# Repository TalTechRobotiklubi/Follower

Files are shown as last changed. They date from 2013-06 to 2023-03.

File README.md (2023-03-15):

Follower
===================
General
-----------
Follower is a robot-platform intended to follow a certain person. The long term goal is to develop a platform, which could act as a personal carrier.
Current repository mainly tracks software, but here are also some documentation.

Concept
-----------
Follower's conceptional drawing is presented below

pilt robotist

The robot has differential drive with two wheels inside the body to avoid collision effect while turning. Sensor boards reads ultrasonic sensors, which should detect any obstacles and inertial measurement unit, which helps to detect robots movements in time (turning, acceleration). Vision board controls servo motors to move camera left/right and up/down.

The robot does not have any basket to carry things. It is a first prototype to 
test following concept.

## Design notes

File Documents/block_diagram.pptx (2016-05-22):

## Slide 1

PC (Zotac)
ensor Board

USB

Kinect ONE

PWM

Servo
ensor Board

2x

USB

VisionBoardr B(STM32F4)

5V

8x

URFs Board

CAN

2 IO

SensorBoard
(STM32F4)
ensor Board

USART

XRF
ensor Board

IMUs Board

USART

5 V

12 V

Motor Controller
ensor Board

Motor Controller
ensor Board

Vbat

Power module
ensor Board

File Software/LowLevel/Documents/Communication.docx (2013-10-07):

TTÜ Robotiklubi MTÜ

12

ITKiller kommunikatsioon

Kommunikatsiooniprotokoll

TTÜ Robotiklubi MTÜ

Sisukord

# Arhitektuur

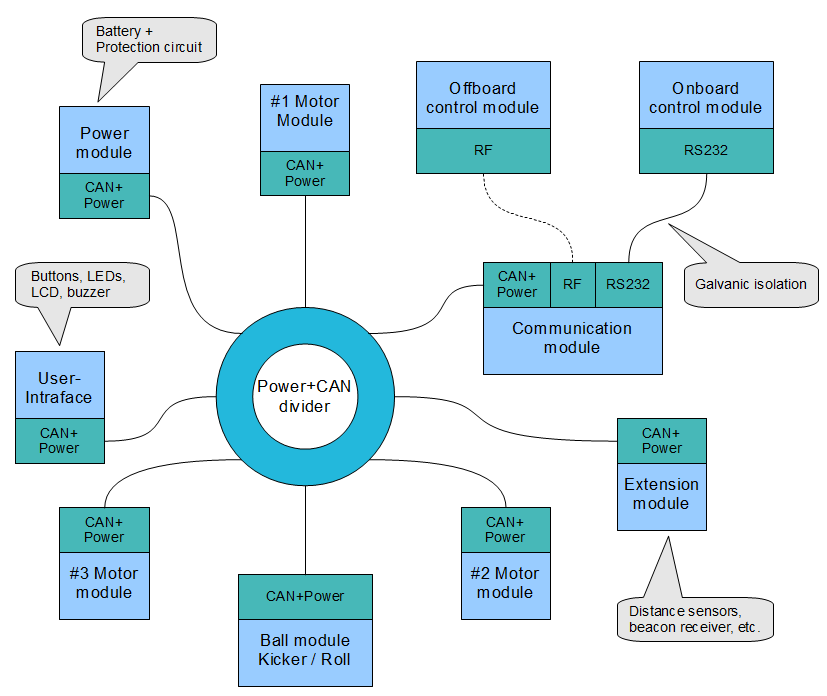
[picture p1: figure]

Roboti “targad” moodulid suhtlevad omavahel CAN siinil. Et PC saaks CAN-iga ühendada, on CAN siinil spetsiaalne kommunikatsioonimoodul mis teisendab CAN sõnumid UART sõnumiteks ja vastupidi:

UART
Kommunikatsiooni-moodul
CAN
PC

UART siinil on kommunikatsiooniprotokolli aluseks võetud CAN. Ehk teisisõnu UART siinil edastatakse peaaegu sama struktuuri ja sisuga sõnumeid nagu CAN siinil. Vahe on ainult sõnumi paketi ülesehituses, mis CAN-i puhul on standardiga ära määratud, UART-i puhul tehtud selles dokumendis.

## CAN liides

Kasutusel on CAN 2.0A standard. Seega ID väli on 11 bitine, kuid kasutatal on sellest ainult 8 madalamat bitti. Kolm kõrgemat bitti on 0. Bitikiirus on 250 kbit/s. Sampling point 75%.

## Jadaliidese

UART/RS232 siinil edastatakse mõlemas suunas samasuguse ehitusega pakette. Pakett mis on saadetud PC-st jadaliidese kaudu CAN siinile, sealt tagasi ei saadeta (ei peegeldu).

Bait | Sisu | Väärtus
0 | Preambula | 0xAA
1 | Sõnumi ID | 0x00 - 0xFF
3 | Sisu pikkus baitides (N) | 1-8
4 | Sisu, ehk signaalid (1..N baiti) | N * 0x00 – 0xFF
5
…
3+N
4+N | Kontrollsumma (16-bit CRC) | 0x00 – 0xFFFF
5+N

Preambula (väärtus 0xAA) on kasutusel sõnumi alguse leidmiseks jadaliidese andmevoost. Preambulale järgneb sõnumi identifikaator (ID) mis on üks-ühele vastavuses CAN sõnumite ID väljaga (8 madalamat bitti sellest). Sõnumi sisu pikkus on 1 bait, millel võib olla väärtuseks 1-8, muul juhul loetakse sõnum vigaseks. Sõnumi sisu on määratud sõnumi ID-ga. Sisus peab olema niipalju baite kui pikkuses kirjas on.

Paketi lõpus on kogu kontrollsumma, millesse arvutatakse sisse sõnumi ID, sisu pikkus ja sisu baidid. CRC algoritm on veel defineerimisel. Arvutatud kontrollsumma ja paketis sisalduvad kontrollsumma mittekattumisel sõnumit ignoreeritakse.

## Sõnumid ja signaalid

Sõnumitel puudub saatja ja addressaat, selle asemel on sõnumil identifikaator (ID) mille alusel sõnumit ja selle sisu tuvastada. CAN ja UART siinil jõuavad kõik sõnumid kõigi mooduliteni. Iga moodul otsustab kas ta on sõnumist huvitatud või mitte. Üldjuhul on siiski määratud mis moodul mis sõnumit saadab.

Sõnumi sisuks on signaalid, ehk ainuühikulised andmed. Signaal võib olla näiteks nupu olek, mootori kiirus või midagi muud mis tähistab ühe kindla funktsiooni reaalset või soovitud olekut. Seega saab sõnumitega edastada olekusignaale ja juhtsignaale.

Signaalide andmehulk on bitipõhine ja nende jaoks on sõnumis reserveeritud täpselt vajalik hulk bitte. Sõnumite kirjelduses on signaalide juures märgitud nende algusbitt ja pikkus. Baidis loendatakse bitte alates vanimast. Ehk näiteks 2-bitine signaal, mille algbiti number on 10 asub teise baidi kolmandas ja neljandas bitis. Sõnumist signaali leidmiseks oleks selle mask 0xC00.

Kokku on ühes sõnumis 1-8 baiti, ehk 8-64 bitti. Bitte loendatakse alates nullist.

# Sõnumid

Järgnevalt on loetletud kõik roboti moodulitevahelised sõnumid

ID | Sõnumi nimi | Selgitus | Saatja | Periood
0xD0 | MotorSpeeds | Kolme mootori sõidukiiruse ühissõnum. | PC | 10 ms
0xD1 | Motor1Status | Esimese mootori hetkekiirus, vool, temperatuur. | Mootor 1 | 100 ms
0xD2 | Motor2Status | Teise mootori hetkekiirus, vool, temperatuur. | Mootor 2 | 100 ms
0xD3 | Motor3Status | Kolmanda mootori hetkekiirus, vool, temperatuur. | Mootor 3 | 100 ms
0xD4 | MotorPID | PID konstantide P, I ja Dmääramine | PC | -
0xB0 | BallControl | Pallimooduli juhtsignaalid. | PC | 20 ms
0xB1 | BallStatus | Pallimooduli olekusignaalid. | Pallimoodul | 20 ms
0xB2 | LineStatus | Eesmiste jooneandurite olek | Pallimoodul | 20 ms
0xC0 | UIControls | Nuppude olekusignaalid. | Komm. moodul | 100 ms
0xC1 | UIFeedback | Indikaator LED-ide ja kõlari juhtsignaal. | PC | -
0xC2 | UIScreenClear | Ekraani kustutamine. | PC | -
0xC3 | UIScreenWrite | Ekraanile kirjutamine. | PC | -
0xA0 | PowerStatus | Aku seisukord. | Komm. moodul | 1000 ms
0xF0 | Sensors | Sensorite tulemused | | 20 ms

Iga sõnum on eraldi lahti seletatud. Sõnumi periood näitab aega, mille tagant sõnumit peab (peaks) kindlaksmääratud saatja seda saatma. Perioodid tuleb ka reaalse sideliidese läbilaskevõimega vastavusse seada. Kui moodulid, mis ootavad kindlat sõnumit, ei saa seda 10 kordse nominaalperioodi jooksul võivad nad ohutuse mõttes välja lülituda, seisma jääda vmt. Sõnumeid, millel pole perioodi määratud, saadetakse vastavalt vajadusele.

## 0xD0 - MotorSpeeds

Mootorite kiiruste seadmise sõnum.

Bitt | Pikkus | Tüüp | Ühik | Signaali nimi | Selgitus
0 | 16 | int16 | rpm | Motor1RequestSpeed | Mootori 1 soovitud pöörlemiskiirus
16 | 16 | int16 | rpm | Motor2RequestSpeed | Mootori 2 soovitud pöörlemiskiirus
32 | 16 | int16 | rpm | Motor3RequestSpeed | Mootori 3 soovitud pöörlemiskiirus

Mootorid on eeldatud asetsema järgneva joonise alusel, kus joon keskel näitab roboti eeldatavat edasiliikumise suunda. Mootorite pöörlemise positiivne suund määratakse parema käe reegliga, kus mootorist ümbert kinni võttes pöial osutab ratta poole ning ülejäänud sõrmed näitavad positiivset pöörlemise suunda. Negatiivne pöörlemise suund on vastupidine positiivsele.

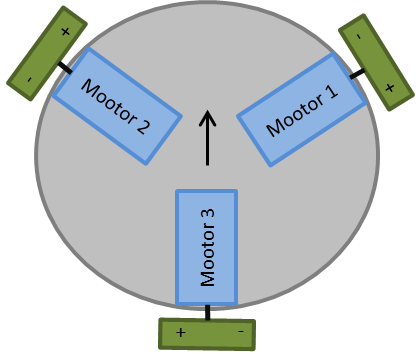
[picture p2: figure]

Mootorite kiiruse sõnumis on kolm 16-bitist signaali, mis tähistavad mootori (mitte ratta) pöörlemiskiirust väärtustes -32768 kuni +32767. Pluss tähistab positiivset pöörlemiskiirust, miinus tähistab negatiivset pöörlemiskiirust. Reaalselt saavutatav kiirus on loomulikult madalam ja see peaks olema tarkvaras konstandina kirjas.

## 0xD1 – Motor1Status, 0xD2 – Motor2Status ja 0xD3 – Motor3Status

Mootori staatuse kirjeldamise sõnum. Kõigis sõnumites on signaalidel samad nimed, aga mootorite indeksid on kas 1, 2 või 3.

Bitt | Pikkus | Tüüp | Ühik | Signaali nimi | Selgitus
0 | 16 | int16 | rpm | Motor1ActualSpeed | Mootori 1 reaalne pöörlemiskiirus
16 | 16 | Int16 | - | Motor1EncoderClicks | Mootori 1 enkoodri muutus viimasest sõnumist.
32 | 8 | uint8 | 100 mA | Motor1CurrentDraw | Mootori 1 voolutarve
40 | 8 | uint8 | °C | Motor1DriverTemp | Mootorikontrolleri 1 temperatuur
48 | 1 | bool | T/F | Motor1BridgeAFault | Mootorikontrolleri 1 poolsilla A viga
49 | 1 | bool | T/F | Motor1BridgeBFault | Mootorikontrolleri 1 poolsilla B viga
50 | 6 | - | - | - | Reserveeritud diagnostikaks

Kolm mootorite olekusõnumit on samasuguse ülesehitusega. Sõnumite signaalid annavad infot mootorite töö kohta. Voolutarve on 100 mA ühikutes, ehk binaarväärtusele 35 vastaks 3,5A.

## 0xD4 - MotorPID

Mootoritele PID konstantide P, I ja D seadmine.

Bitt | Pikkus | Tüüp | Ühik | Signaali nimi | Selgitus
0 | 32 | uint32 | - | ConstantAddress | STM32 kontrolleri mälu aadress
32 | 32 | uint32 | - | ConstantValue | P, I või D väärtus

## 0xB0 – BallControl

Pallimooduli juhtsignaalid.

Bitt | Pikkus | Tüüp | Ühik | Signaali nimi | Selgitus
0 | 1 | bool | T/F | BallCharge | Kondesaatori laadimise lubamine.
1 | 7 | uint8 | % | BallDribblerPower | Rullimootori PWM tööaeg.
8 | 10 | uint16 | ms | BallKickTime | Solenoidi löögiaeg.
18 | 1 | bool | T/F | BallKick | Solenoid löömine.

BallCharge kaudu juhitakse kondensaatori laadimisskeemi tööd. Tõese väärtus (1) puhul on automaatne laadimine lubatud, väära (0) puhul mitte. Kui laadimine keelatakse, siis kondensaatori laadimine peatatakse, kuid seda ei tühjendata.

BallKick kaudu antakse käsk palli löömiseks solenoidiga. Tõese väärtus (1) puhul on palli löömiskäsk antud, väära (0) puhul mitte. Kui väärtus jätta tõeseks, siis tehakse löök automaatselt kondensaatori laadimise lõppedes. Seega ühekordseks löögiks peab väärtuse enne laadimise lõppemist ära nullima.

BallKickTime kaudu määratakse solenoidi transistori lahtioleku aeg. See mõjutab löögi aega ja tugevust. Väärtus on 0-1023 millisekundit.

BallDribblerPower määrab rulli mootori töötsükli aja protsentides. Väärtuse 0 puhul mootor seisab, väärtuse 100 (või suurema) puhul töötab maksimaalse võimsusega.

## 0xB1 – BallStatus

Pallimooduli olekusignaalid.

Bitt | Pikkus | Tüüp | Ühik | Signaali nimi | Selgitus
0 | 1 | bool | T/F | BallContact | Rullianduri olek (kontakt palliga).
1 | 1 | bool | T/F | BallInSight | Optilise palli anduri olek.
2 | 1 | bool | T/F | BallCapacitorCharged | Kondensaatori laetuse olek.

BallContact näitab kas pall (või muu objekt) on rulli all. Tõene väärtus (1) puhul on rull tõusnud, 0 (False) puhul mitte.

BallInSight on optilise pallianduri olek. Optiline andur peaks nägema palli mõned sentimeetrid enne rulli. Tõene väärtus (1) näitab, et palliandur näeb palli või muud objekti, väär (0) vastupidist.

BallCapacitorCharged on löögielektroonika kondensaatori laetuse olek. Tõese väärtuse (1) puhul on kondensaator täielikult laetud, väära (0) puhul (veel) mitte.

## 0xB2 – LineStatus

Jooneandurite olekusignaalid.

Bitt | Pikkus | Tüüp | Ühik | Signaali nimi | Selgitus
0 | 8 | uint8 | % | LineLeftIntensity | Vasaku jooneanduri intensiivsus.
8 | 8 | uint8 | % | LineRightIntensity | Parema jooneanduri intensiivsus.

LineLeftIntensity ja LineRightIntensity näitavad optilistesse peegeldusanduritesse tagasipeegeldunud valguse intensiivust. Väärtuse 0% puhul on valguse intensiivsus minimaalne (optotransistor on suletud), väärtuse 100% puhul on valguse intensiivsus maksimaalne (optotransistor on täielikult avatud).

## 0xC0 – UIControls

Juhtpaneeli juhtliideste olekud.

Bitt | Pikkus | Tüüp | Ühik | Signaali nimi | Selgitus
0 | 1 | bool | T/F | ButtonTopLeft | Ülemise vasaku nupu olek.
1 | 1 | bool | T/F | ButtonTopRight | Ülemise parema nupu olek.
2 | 1 | bool | T/F | ButtonBottomLeft | Alumise vasaku nupu olek.
3 | 1 | bool | T/F | ButtonBottomRight | Alumise parema nupu olek.

ButtonTopLeft, ButtonTopRight, ButtonBottomLeft ja ButtonBottomRight on kommunikatsioonimooduli paneelil olevate nuppude olekud. Tõese väärtuse (1) puhul on nupp alla vajutatud, väära (0) puhul mitte.

## 0xC1 – UIFeedback

Juhtpaneeli tagasisidefunktsioonide käsud.

Bitt | Pikkus | Tüüp | Ühik | Signaali nimi | Selgitus
0 | 8 | uint8 | ms | LEDRed | Punase valgusdioodi põlemise aeg.
8 | 8 | uint8 | ms | LEDGreen | Rohelise valgusdioodi põlemise aeg.
16 | 16 | uint16 | Hz | BeepFrequency | Piiksu sagedus.
32 | 8 | uint8 | ms | BeepDuration | Piiksu pikkus.

LEDRed ja LEDGreen signaalid juhivad vastavalt punase ja rohelise valgusdioodi põlemise aega. Väärtuste 1 ms ja suuremate puhul põleb valgusdiood vastava aja alates sõnumi kättesaamisest. Väärtuse 0 puhul valgusdioodi ei juhita, ehk sellega saab lasta eelmisel valgusdioodi käsul edasi toimida.

BeepFrequency määrab ära soovitud helisignaali sageduse. Väärtus on 0 kuni 65535 hz, kuid loomulikult sõltub saavutatav helikõrgus kõlarist. Reaalne väärtus on 500 hz kuni 5000 hz.

BeepDuration määrab kas teha helisignaal (piiks) ja kui pikk. Väärtuse 1 ms ja suuremate väärtuste puhul kostab signaal vastava aja alates sõnumi saabumisest. Väärtuse 0 puhul heli ei tehta ja kui sõnumi saabumisel pole eelmine helisignaal lõppenud, siis seda ei peatata kah. Kui eelmine helisignaal pole lõppenud ja tuleb käsk uue jaoks, siis alustatakse koheselt uue signaaliga.

NB. Aku tühjenemise korral võib juhtmoodul helisignaali käskusid ignoreerida ja kasutada automaatset hoiatussignaali.

## 0xC2 – UIScreenClear

Juhtpaneeli ekraanil rea kustutamise sõnum. Kokku on ekraanil 4 rida.

Bitt | Pikkus | Tüüp | Ühik | Signaali nimi | Selgitus
0 | 3 | uint8 | - | ScreenRow | Ekraani rea number.

ScreenRow näitab rida, mis tekstist kustutada. Väärtuste 0 kuni 3 puhul kustutatakse rida 1 kuni 4. Ridasid loetakse ülevalt alla. Väärtuse 4 kuni 7 korral kustutatakse kogu ekraan.

## 0xC3 – UIScreenWrite

Juhtpaneeli ekraanile teksti kirjutamise sõnum. Ekraanile mahub 4 rida 16-märgist ASCII kodeeringus teksti. Teksti saab vanast tekstist üle kirjutada.

Bitt | Pikkus | Tüüp | Ühik | Signaali nimi | Selgitus
0 | 4 | uint8 | - | ScreenRow | Ekraani rea number.
4 | 4 | uint8 | - | ScreenColumn | Ekraani tulba number.
8 | 4 | uint8 | - | ScreenTextLen | Teksti pikkus mida kirjutada (1-6)
16 | 48 | char | | ScreenText | Tekst (6 märki)

ScreenRow näitab rida millele tekst kirjutada. Väärtused 0 kuni 3 tähistavad ridu 1 kuni 4. Ridasid loetakse ülevalt alla.

ScreenColumn näitab tulpa millest alates teksti kirjutada. Tulpasid loetakse vasakult.

ScreenTextLen näitab mitu märki sõnumis olevast tekstist ekraanile kirjutada. Kuna sõnumi pikkus on deterministlikusse säilitamiseks fikseeritud, siis pikkust määrab see signaal. Väärtuse 0 puhul kirjutatakse ekraanile üks (esimene) märk, väärtuse 5 (või suurem) puhul kõik 6 märki.

ScreenText sisaldab ASCII kodeeringus 6-märgilist teksti. Kui kirjutatada soovitakse vähem kui 6 märki, siis ülejäänud märgid võivad olla 0xFF. Seda kas kasutada saab kogu ASCII tabelit, sõltub kommunikatsioonimoodulist. Suur ja väike ladina tähestik, numbrid ja kirjavahemärgid peaksid kindlasti toetatud olema.

## 0xA0 - PowerStatus

Aku seisundi olekusõnum.

Bitt | Pikkus | Tüüp | Ühik | Signaali nimi | Selgitus
0 | 16 | uint16 | mV | Battery1Voltage | Aku 1 (mootorite aku) pinge.

Battery1Voltage näitab aku 100 ms jooksul keskmistatud pinget. Väärtused on 0 kuni 65535 mV.

## 0xF0 – Sensors

Sensorite näitude sõnum.

Bitt | Pikkus | Tüüp | Ühik | Signaali nimi | Selgitus
0 | 8 | uint8 | cm | DistanceSensor1 | Distantsisensori 1 kaugusnäit.
8 | 8 | uint8 | cm | DistanceSensor2 | Distantsisensori 2 kaugusnäit.
16 | 8 | uint8 | cm | DistanceSensor3 | Distantsisensori 3 kaugusnäit.
24 | 8 | uint8 | cm | DistanceSensor4 | Distantsisensori 4 kaugusnäit.
32 | 8 | uint8 | cm | DistanceSensor5 | Distantsisensori 5 kaugusnäit.
40 | 8 | uint8 | cm | DistanceSensor6 | Distantsisensori 6 kaugusnäit.
48 | 8 | uint8 | cm | DistanceSensor7 | Distantsisensori 7 kaugusnäit.
56 | 8 | uint8 | cm | DistanceSensor8 | Distantsisensori 8 kaugusnäit.

Distancesensor signaal näitab kaugust sentimeetrites.

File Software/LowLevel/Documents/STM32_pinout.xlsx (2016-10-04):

 |  |  |  |  |  |  |  |  |  | free
 |  |  |  |  |  |  |  |  |  | occupied by kit
 |  |  |  |  |  |  |  |  |  | used by follower
 |  |  |  |  |  |  |  |  |  | occupied by kit / used by follower
 |  |  | STM32 pinout
follower | kit function |  |  |  | follower | follower | kit function |  |  | kit function | follower
 |  | GND | GND |  |  |  |  | GND | GND
 |  | VDD | VDD |  |  |  |  | 5V | 5V
 |  | GND | NRST |  |  |  |  | 3V | 3V
 |  | PC1 | PC0 |  |  |  | OSC_IN | PH0 | PH1 | OSC_OUT
 |  | PC3 | PC2 |  |  | URF1 echo |  | PC14 | PC15 |  | URF1 trig
 |  | PA1 | PA0 | user button |  | URF2 echo |  | PE6 | PC13 |  | URF2 trig |  |  | xRF
USART2_RX / XRF_Rx |  | PA3 | PA2 |  | USART2_TX / XRF_Tx | URF3 echo |  | PE4 | PE5 |  | URF3 trig |  |  | pin 2 | receive
 | acceler SPI | PA5 | PA4 |  |  | URF4 echo |  | PE2 | PE3 | CS_I2C/SPI |  |  |  | pin 3 | transmit
 | acceler SPI | PA7 | PA6 | acceler SPI |  |  | acceler INT1 | PE0 | PE1 | acceler INT2
URF5 echo |  | PC5 | PC4 |  | URF5 trig | URF4 trig |  | PB8 | PB9 | I2C1_SDA
URF6 echo |  | PB1 | PB0 |  | URF6 trig |  |  | BOOT0 | VDD
 |  | GND | PB2 |  |  |  | I2C1_SCL | PB6 | PB7 |  |  |  |  | XRF plaat top view
URF7 echo |  | PE7 | PE8 |  | URF7 trig |  |  | PB4 | PB5 |  |  | 1 | 2 | 3 | 4 | 5 | 6 | 7 | 8
URF8 echo |  | PE9 | PE10 |  | URF8 trig |  |  | PD7 | PB3 |  |  | gnd |  | Rx | Tx | gnd | 3,3V
 |  | PE11 | PE12 |  |  |  |  | PD5 | PD6
 |  | PE13 | PE14 |  |  |  |  | PD3 | PD4 | reset
 |  | PE15 | PB10 |  |  | CAN1_Tx |  | PD1 | PD2
 |  | PB11 | PB12 |  |  |  |  | PC12 | PD0 |  | CAN1_Rx
 |  | PB13 | PB14 |  |  | UART4_Tx | SCLK | PC10 | PC11 |  | UART4_Rx |  |  |  | XRF
 |  | PB15 | PD8 |  |  |  |  | PA14 | PA15
 |  | PD9 | PD10 |  |  |  |  | PA10 | PA13
 |  | PD11 | PD12 | green LED |  |  | I2C3_SCL | PA8 | PA9 | Vbus green LED
 | orange LED | PD13 | PD14 | red LED |  | stop switch |  | PC8 | PC9 | I2C3_SDA
 | blue LED | PD15 | NC |  |  |  |  | PC6 | PC7 | CS43L22 MCLK
 |  | GND | GND |  |  |  |  | GND | GND

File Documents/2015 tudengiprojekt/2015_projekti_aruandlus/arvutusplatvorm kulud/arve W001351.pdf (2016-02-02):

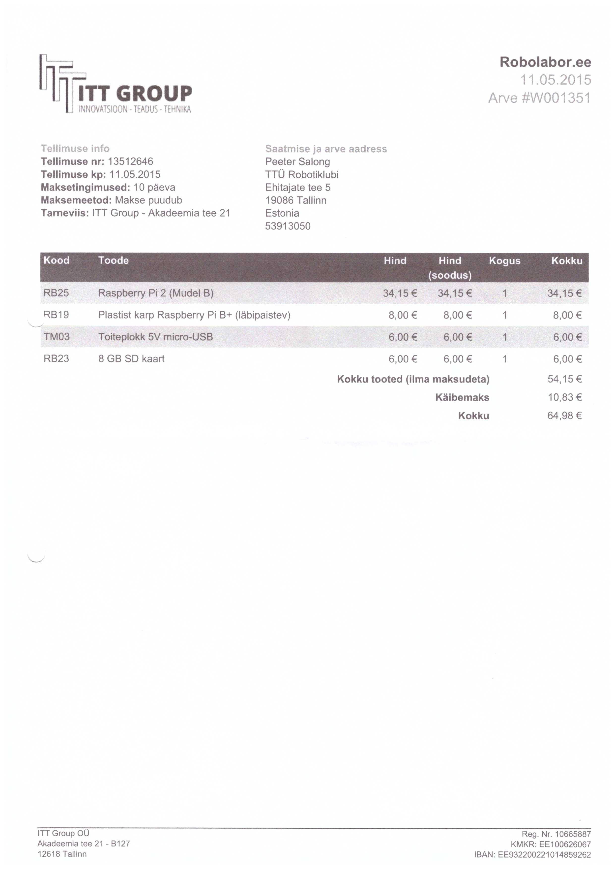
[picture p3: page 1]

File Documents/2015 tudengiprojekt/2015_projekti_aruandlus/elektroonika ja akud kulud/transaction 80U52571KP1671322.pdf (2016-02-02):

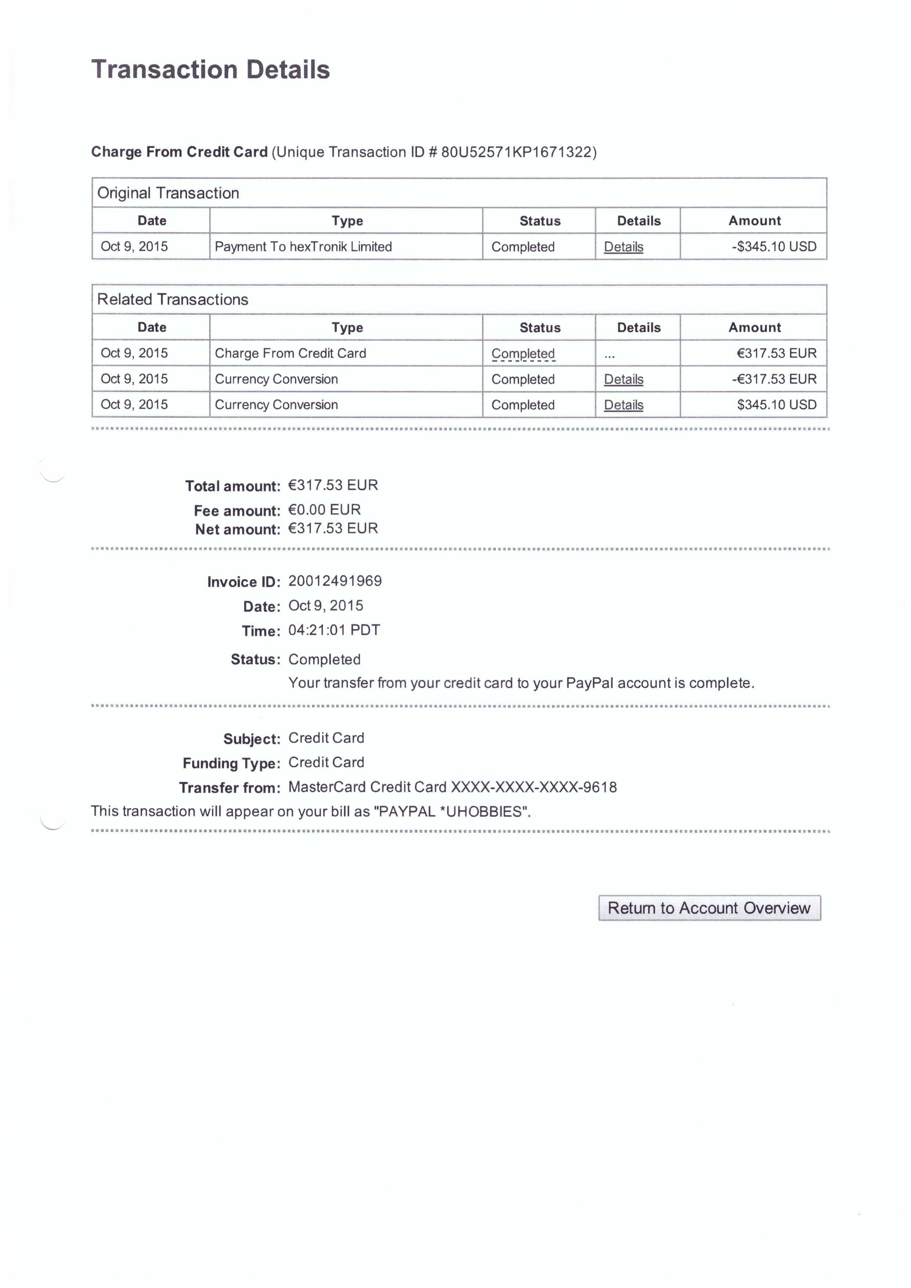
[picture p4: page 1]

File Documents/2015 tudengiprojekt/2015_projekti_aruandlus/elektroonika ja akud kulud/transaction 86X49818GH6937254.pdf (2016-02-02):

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

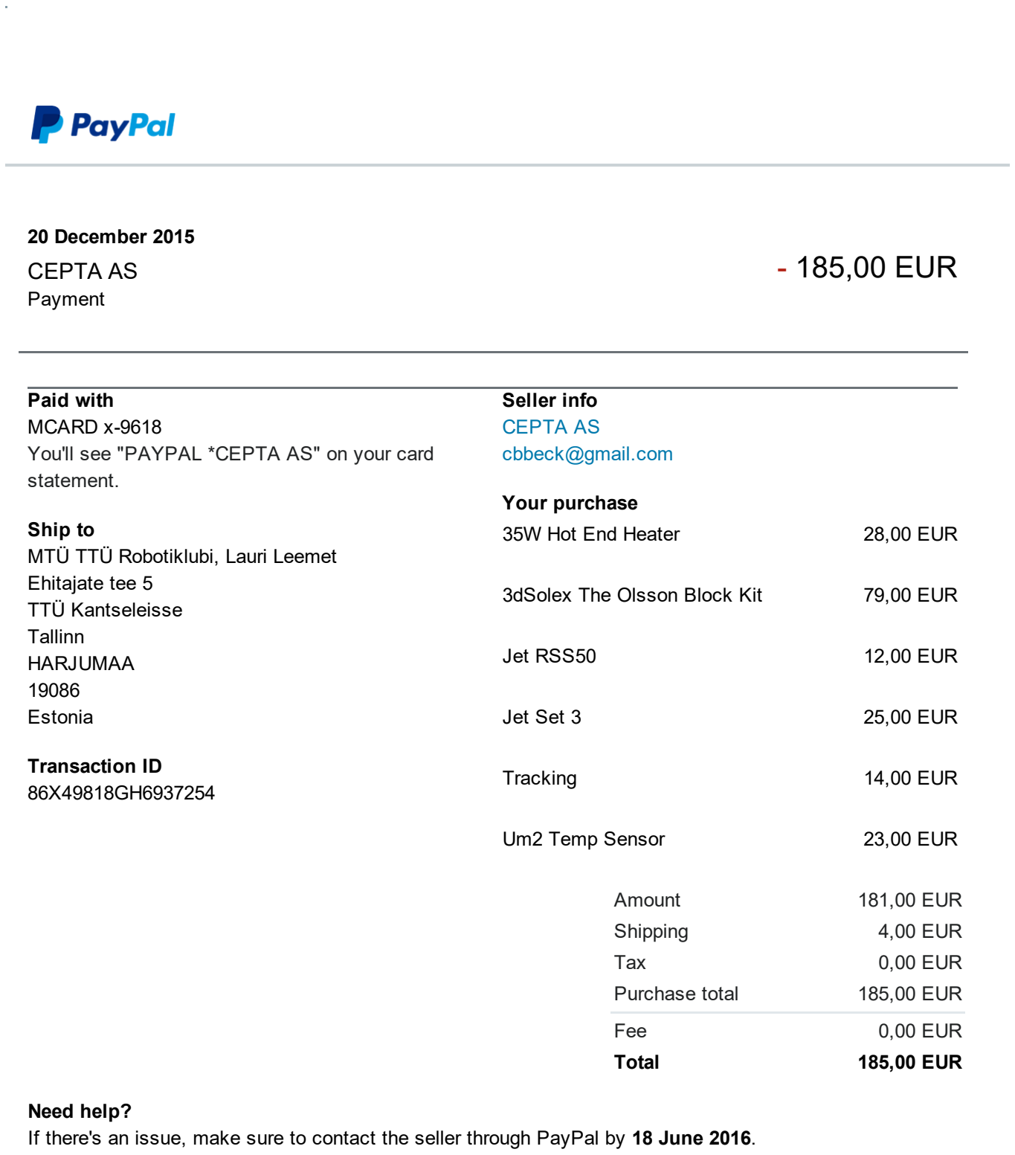
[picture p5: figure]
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

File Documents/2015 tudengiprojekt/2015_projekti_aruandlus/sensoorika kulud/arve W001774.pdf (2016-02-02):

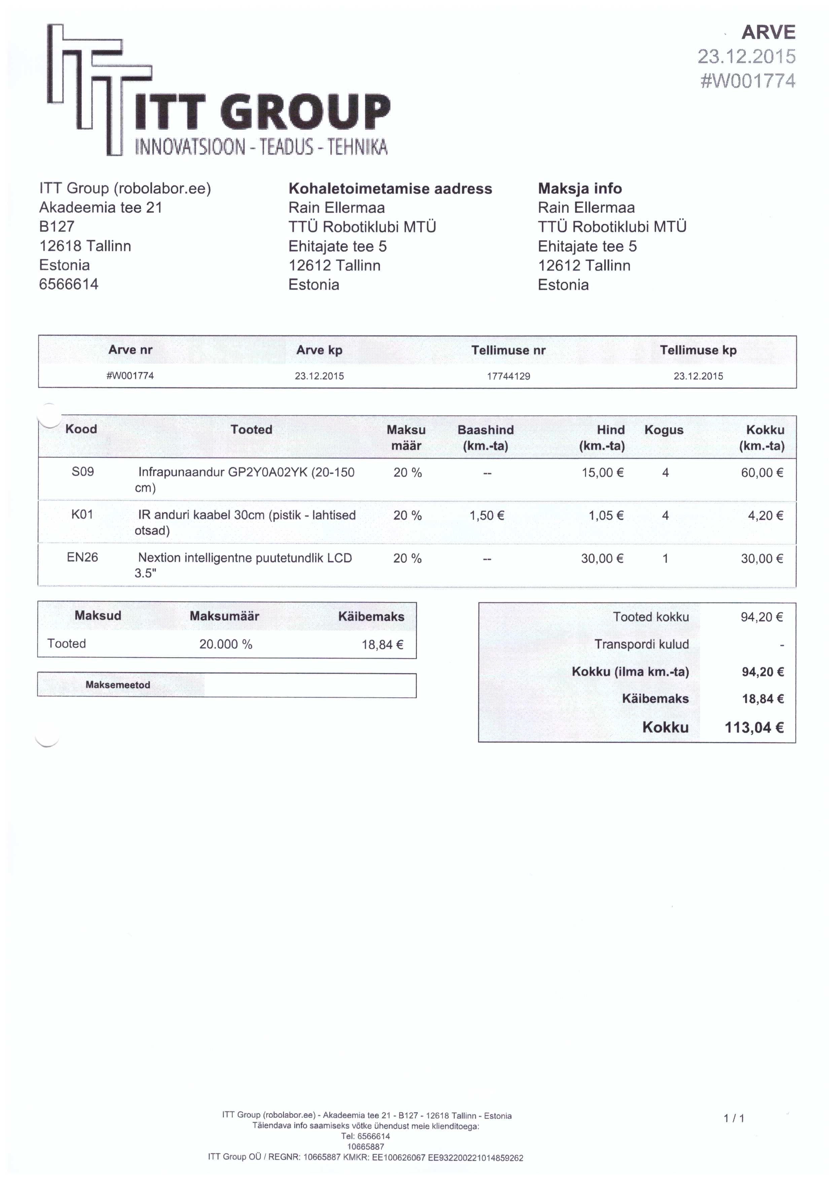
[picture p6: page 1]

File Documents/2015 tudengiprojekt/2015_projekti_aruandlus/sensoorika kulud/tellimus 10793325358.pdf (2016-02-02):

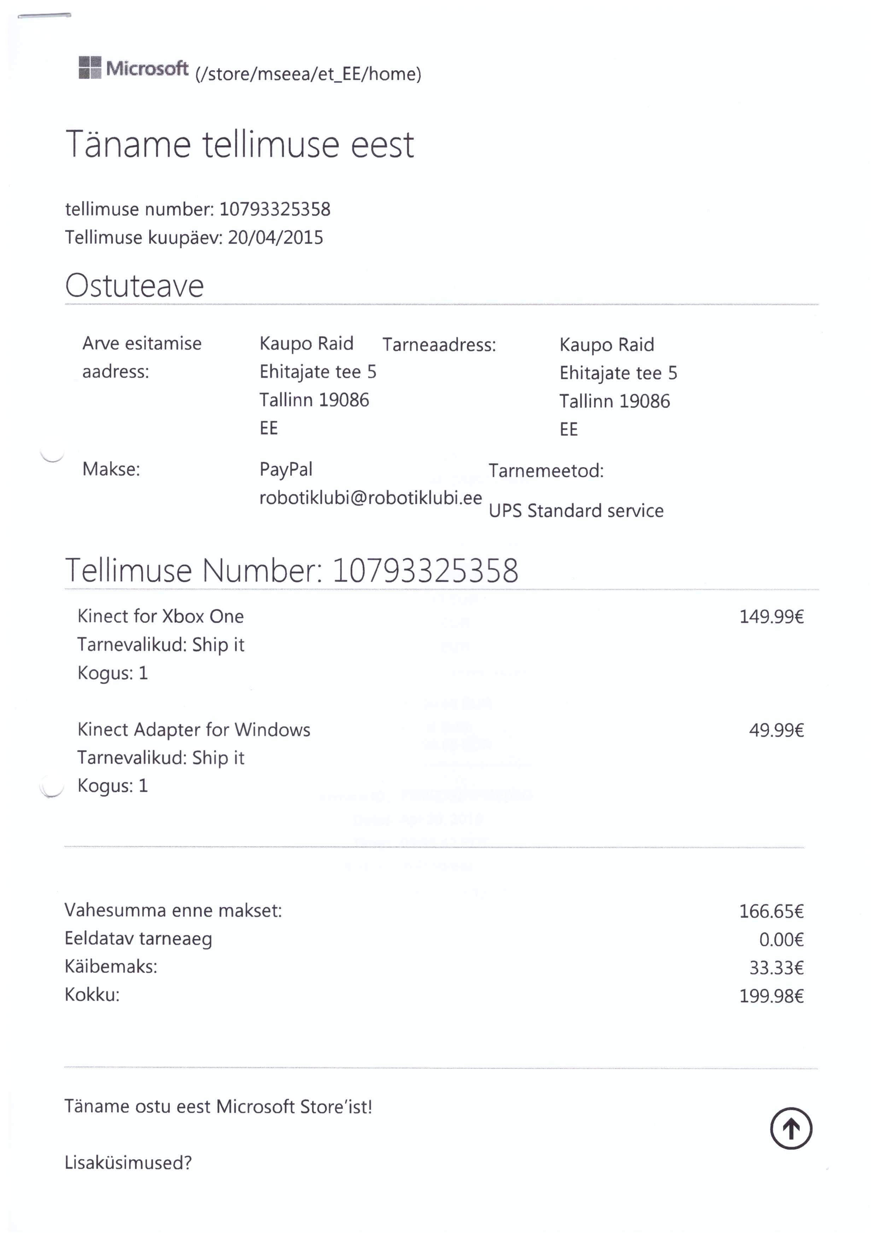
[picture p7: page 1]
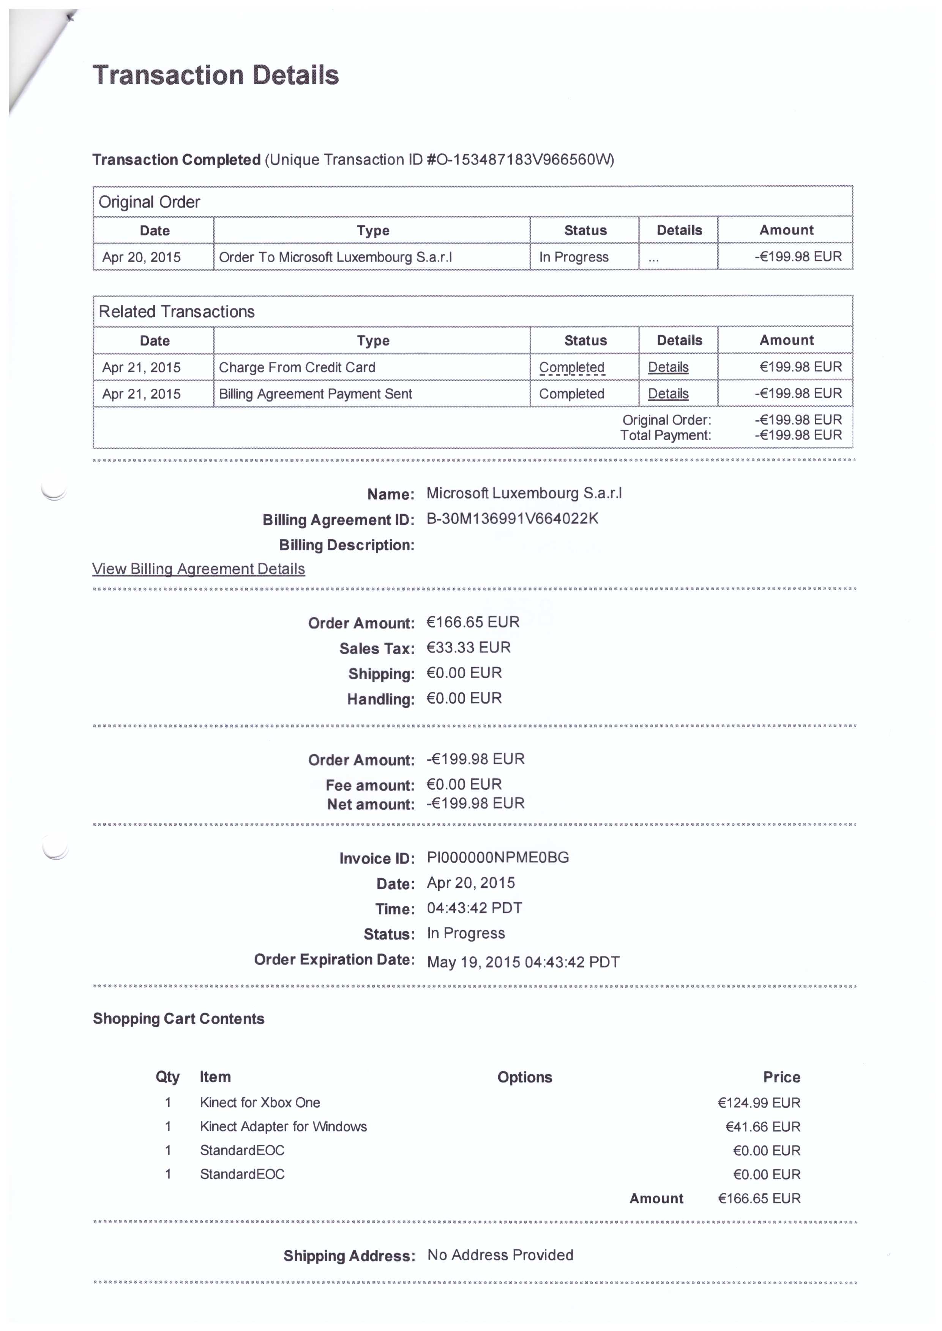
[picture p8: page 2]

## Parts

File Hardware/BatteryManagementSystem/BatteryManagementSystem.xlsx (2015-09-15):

 | LiPo Battery management system
 | Rain Ellermaa
 | BatteryManagementSystem.PrjPCB
 | None
 | 4.05.2014 | 22:23:08
 | 2014-05-04 | 23:50:14
Nr | Description | Comment | Designator | Footprint | Manufacturer | ManufacturerPN | FarnellPN | Quantity | Unit Price | Part Price
1 | Capacitor Ceramic | 1uF | C1B, C2B, C13C, C14C, C15C | C 0603 |  | MC0603X105K250CT | 1759409 | 5 | 0.026 € | 0.130 €
2 | Capacitor Ceramic | 10uF | C1C, C2C, C5C, C8C, C9C, C20C | C 1206 |  | MC1206X106K250CT | 2320887 | 6 | 0.121 € | 0.726 €
3 | Capacitor Ceramic | 100pF | C3B, C4B | C 0603 |  | MC0603N101J500CT | 1759066 | 2 | 0.010 € | 0.020 €
4 | Capacitor Ceramic | 100nF | C3C, C4C, C5B, C6B, C6C, C7B, C7C, C8B, C9B, C10B, C10C, C11B, C12B, C12C, C13B, C17C, C18C, C19C | C 0402 |  |  |  | 18 |  | 0.000 €
5 | Capacitor Ceramic | 56nF | C11C, C16C | C 0603 |  | C0603C563K5RACTU | 1865538 | 2 | 0.014 € | 0.028 €
6 | Capacitor Ceramic | 2.2uF | C21C | C 0805 |  | GRM21BF51E225ZA01L | 9527702 | 1 | 0.105 € | 0.105 €
7 | Diode | BAT54HT1G | D1B, D1C, D2B | SOD323 |  | 1PS76SB10 | 1081179 | 3 | 0.390 € | 1.170 €
8 | LED | Charge in progress | D2C | LED 3.2x1.6 |  | KPT-2012SURCK | 2099241 | 1 | 0.085 € | 0.085 €
9 | Diode Zener | 5.6V | D3B | SOD323 |  | BZT52C5V6S-7-F | 2077936 | 1 | 0.035 € | 0.035 €
10 | LED | Charge complete | D3C | LED 3.2x1.6 |  | KPT-2012SGC | 2099239 | 1 | 0.069 € | 0.069 €
11 | LED | Power good | D4C | LED 3.2x1.6 |  | KP-2012QBC-D | 2217974 | 1 | 0.169 € | 0.169 €
12 | Inductor | 6.8uH | L1C | COIL5 |  | SRP1235-6R8M | 1828109 | 1 | 1.590 € | 1.590 €
13 | Header, 4-Pin | NTC Thermistors | P1B | MHDR1X4 |  | NTCLE203E3103GB0 | 1187036 | 3 | 1.180 € | 3.540 €
14 | Header, 2-Pin | NTC thermistor | P1C | MHDR1X2 |  | NTCLE203E3103GB0 | 1187036 | 1 |  | 0.000 €
15 | Header, 4-Pin | SMBus | P2BMS | MHDR1X4 |  |  |  | 1 |  | 0.000 €
16 | Header, 4-Pin, Right Angle | Balancer | P2L | HDR1X4H |  |  |  | 1 |  | 0.000 €
17 | Resistor | 10k | R1B, R20B, R20C, R21C, R22C, R24C | R 0603 |  |  |  | 6 |  | 0.000 €
18 | Resistor | 0,01R | R1C, R8C | R 1206 |  | LRMAM1206-R01FT5 | 2079442 | 2 | 0.210 € | 0.420 €
19 | Resistor | 100R | R2B, R5B, R6B, R8B, R9B, R10B, R12B, R13B, R13C | R 0603 |  | CRGH0603F100R | 2331989 | 9 | 0.010 € | 0.090 €
20 | Resistor | 2R | R2C | R 1206 |  | MC0125W120612R0 | 2142034 | 1 | 0.061 € | 0.061 €
21 | Resistor | 1k | R3B, R5C, R6C, R7C, R9C | R 0603 |  |  |  | 5 |  | 0.000 €
22 | Resistor | 100k | R3C, R17C, R18C, R19C, R22B | R 0603 |  |  |  | 5 |  | 0.000 €
23 | Resistor | 200R | R4B, R7B | R 0603 |  | CR0603-JW-201GLF | 2333571 | 2 | 0.014 € | 0.028 €
24 | Resistor | 2k | R11B | R 0603 |  | CPF0603F2K0C1 | 1527506 | 1 | 0.049 € | 0.049 €
25 | Resistor | 9,31k | R11C | R 0603 |  | CPF0603F9K31C1 | 1527578 | 1 | 0.049 € | 0.049 €
26 | Resistor | 1M | R12C | R 0603 |  | CRGH0603F1M0 | 2332042 | 1 | 0.010 € | 0.010 €
27 | Resistor | 0,02R | R14B, R15B, R16B, R17B | R 2512 |  | LVK24R020DER | 1462319 | 4 | 1.650 € | 6.600 €
28 | Resistor | 430k | R14C | R 0603 |  | CRCW0603430KFKEA | 2138561 | 1 | 0.007 € | 0.007 €
29 | Resistor | 200k | R15C | R 0603 |  | CR0603-FX-2003ELF | 2333532 | 1 | 0.023 € | 0.023 €
30 | Resistor | 10R | R16C | R 0603 |  | CRGH0603J10R | 2331699 | 1 | 0.008 € | 0.008 €
31 | Resistor | 3M | R18B, R21B | R 0603 |  | MC0063W060313M00 | 2141599 | 2 | 0.029 € | 0.058 €
32 | Resistor | 5.1k | R19B, R23B | R 0603 |  | CR0603-FX-5101ELF | 2333596 | 2 | 0.023 € | 0.046 €
33 | Resistor | 22.1k | R23C | R 0603 |  | CPF0603F22K1C1 | 1527620 | 1 | 0.049 € | 0.049 €
34 | Resistor | 32.4k | R25C | R 0603 |  | ERJ3EKF3242V | 2059455 | 1 | 0.012 € | 0.012 €
35 | Mosfet N-Ch | NTMFS4926NT1G | T1B, T2B, T4C, T5B, T5C, T6B, T7B, T8B | DFN5 |  | NTMFS4926NT1G | 2317608 | 8 | 0.260 € | 2.080 €
36 | Mosfet P-Ch | SI7101DN-T1-GE3 | T1C, T2C | DFN5 |  | SI7101DN-T1-GE3 | 2364059 | 2 | 0.600 € | 1.200 €
37 | Mosfet N-Ch | 2N7002 | T3B | SOT-23 |  | 2N7002 | 1510761 | 1 | 0.039 € | 0.039 €
38 | Mosfet P-Ch | BSS84AK | T4B | SOT-23 |  | BSS84AK | 1972673 | 1 | 0.098 € | 0.098 €
39 | Li-Ion Battery Pack Manager | BQ3055DBTR | U1B | DBT30_N | Texas Instruments |  |  | 1 |  | 0.000 €
40 | Li-Polymer Battery Charger | BQ24610RGER | U1C | RGE24-2450X2450TP | Texas Instruments |  |  | 1 |  | 0.000 €
Total |  |  |  |  |  |  |  |  |  | 18.59 €
 |  |  |  |  |  |  |  |  | Total+KM | 22.31 €

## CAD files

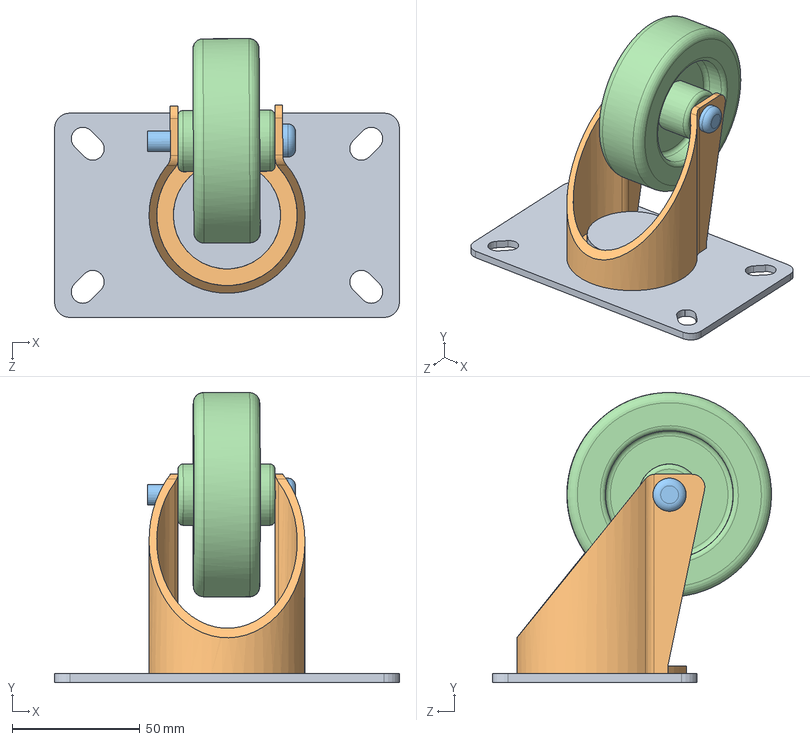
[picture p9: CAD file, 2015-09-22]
Hardware/Body/Esiratas.SLDASM
135.0 x 113.5 x 109.2 mm
Eesratta plaat
Eesratta raam
Eesratta polt
Esiratas

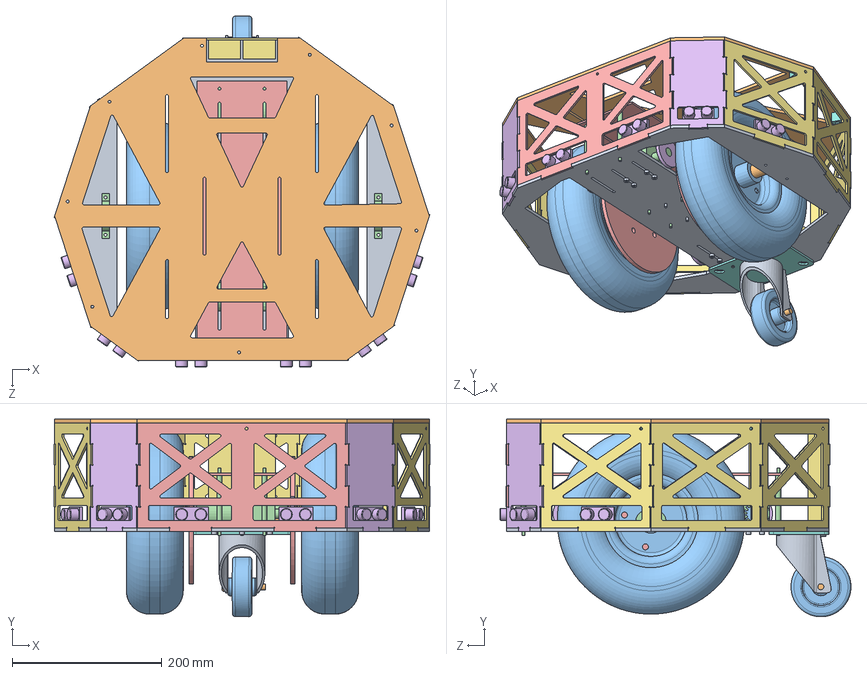
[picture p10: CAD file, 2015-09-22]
Hardware/Body/Koos.SLDASM
501.4 x 263.5 x 468.3 mm
Alus
Telg
Ratas x 2
Mootor x 2
Suur hammasratas x 2
Väike hammasratas x 2
Aku x 2
Eesratta plaat
Eesratta raam
Eesratta polt
Esiratas
Teljekinnitus x 3
Suur külg
Väike külg x 2
Küljeplaat x 7
Kinnitusblokk x 8
4x15 polt x 11
Katus
Enkoodriratas x 2
Sisemine puks x 8
Siseplaat
Ultraheli andur x 6

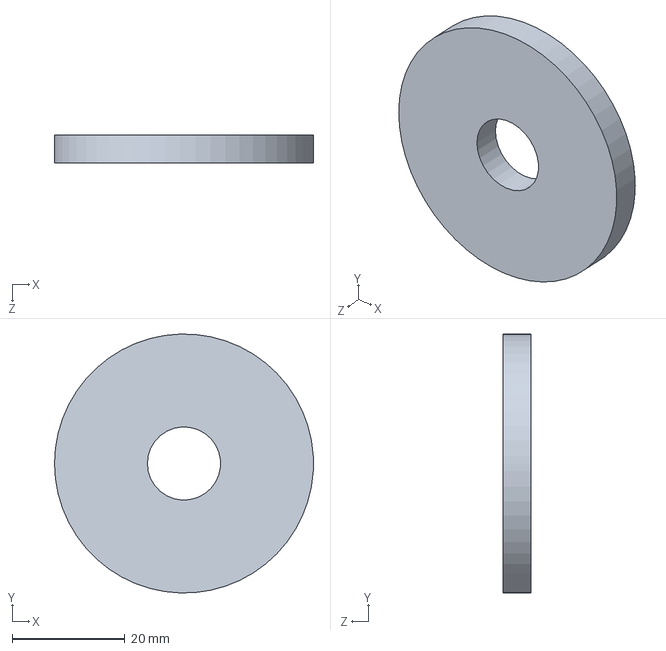
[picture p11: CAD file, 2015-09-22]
Hardware/Body/V�ike hammasratas.SLDPRT
46.0 x 46.0 x 5.00 mm

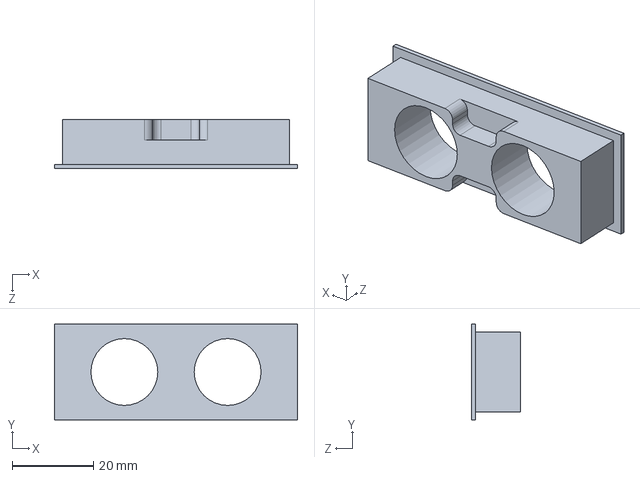
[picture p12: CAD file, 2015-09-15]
Hardware/URF Box/URFBox.SLDPRT
60.0 x 23.7 x 12.0 mm

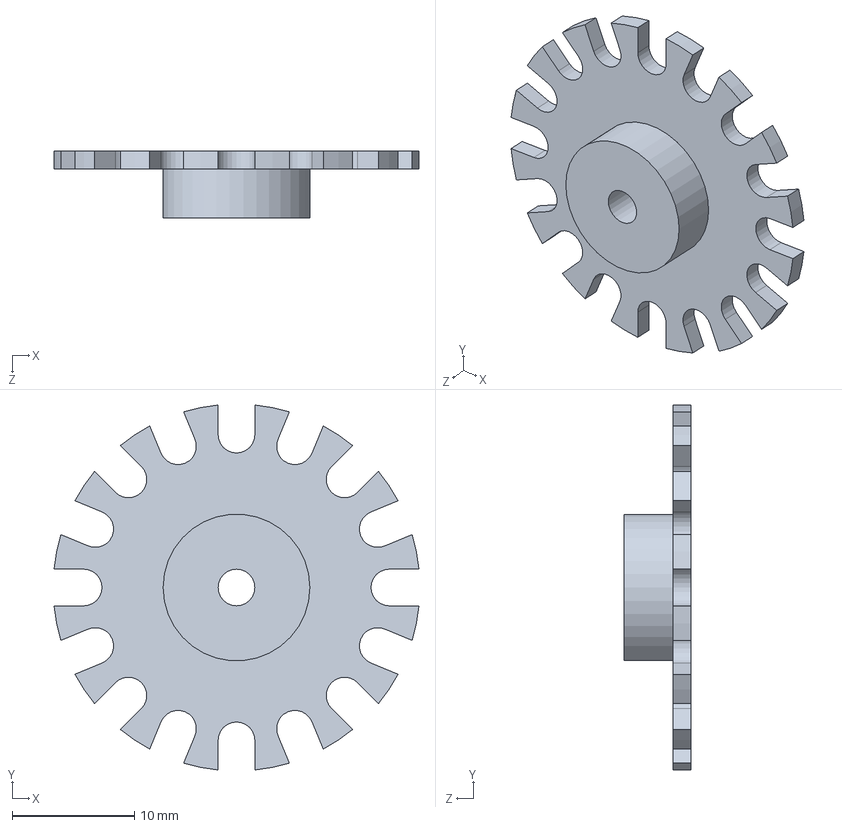
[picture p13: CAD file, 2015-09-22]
Hardware/Body/Enkoodriratas.SLDPRT
29.8 x 29.8 x 5.50 mm

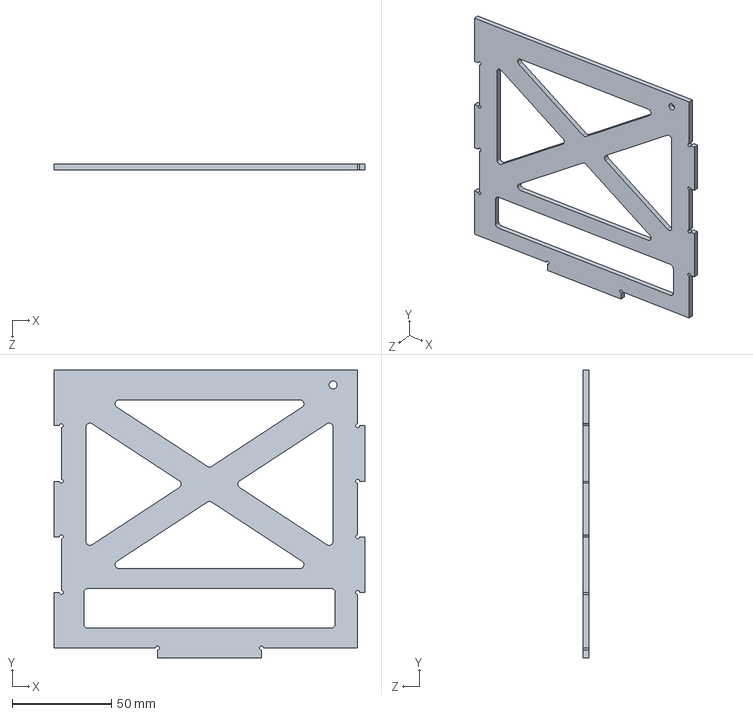
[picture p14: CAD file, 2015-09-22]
Hardware/Body/K�ljeplaat.SLDPRT
156.7 x 145.0 x 3.00 mm

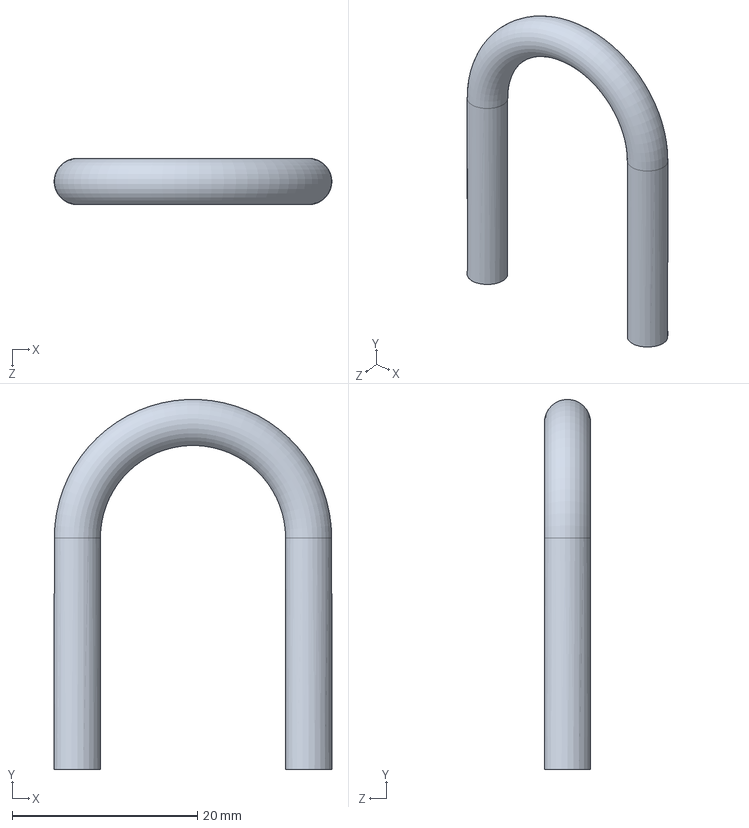
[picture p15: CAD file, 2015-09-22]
Hardware/Body/Teljeklamber.SLDPRT
30.0 x 40.0 x 5.00 mm

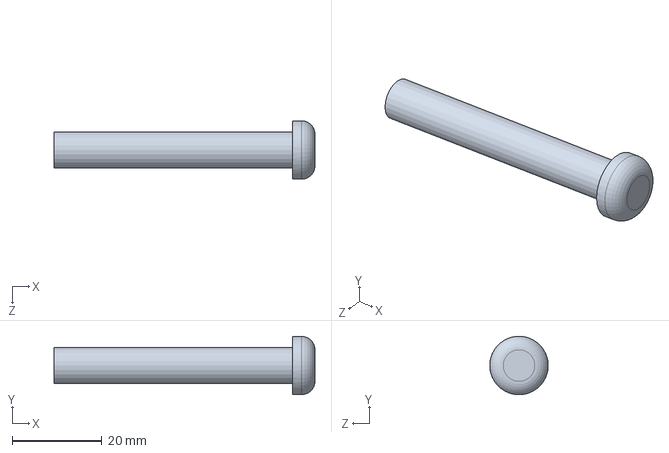
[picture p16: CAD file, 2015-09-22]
Hardware/Body/Eesratta polt.SLDPRT
58.0 x 13.0 x 13.0 mm

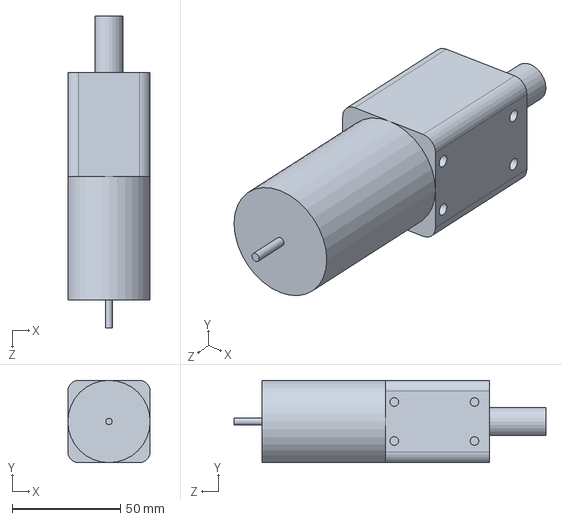
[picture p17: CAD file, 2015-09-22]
Hardware/Body/Mootor.SLDPRT
38.0 x 38.0 x 144.0 mm

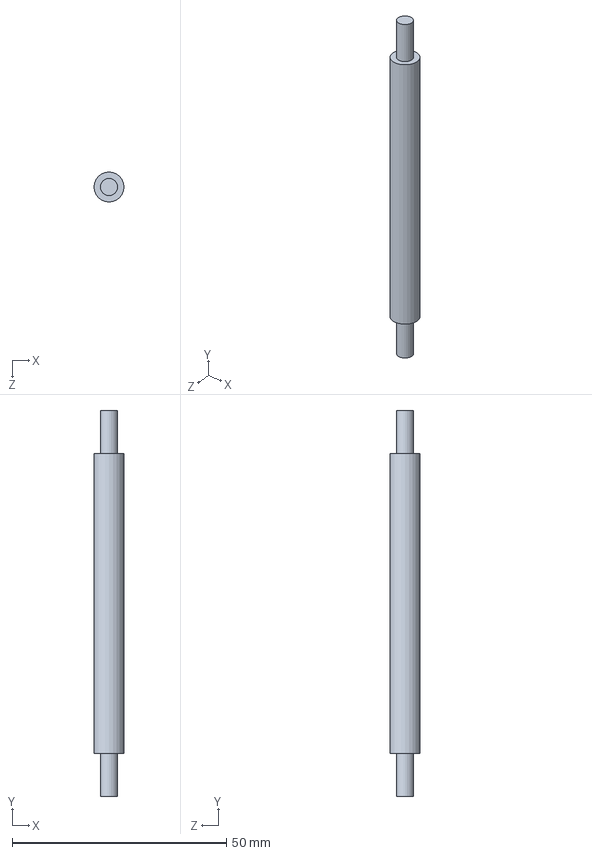
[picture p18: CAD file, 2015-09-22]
Hardware/Body/Sisemine puks.SLDPRT
7.00 x 90.0 x 7.00 mm

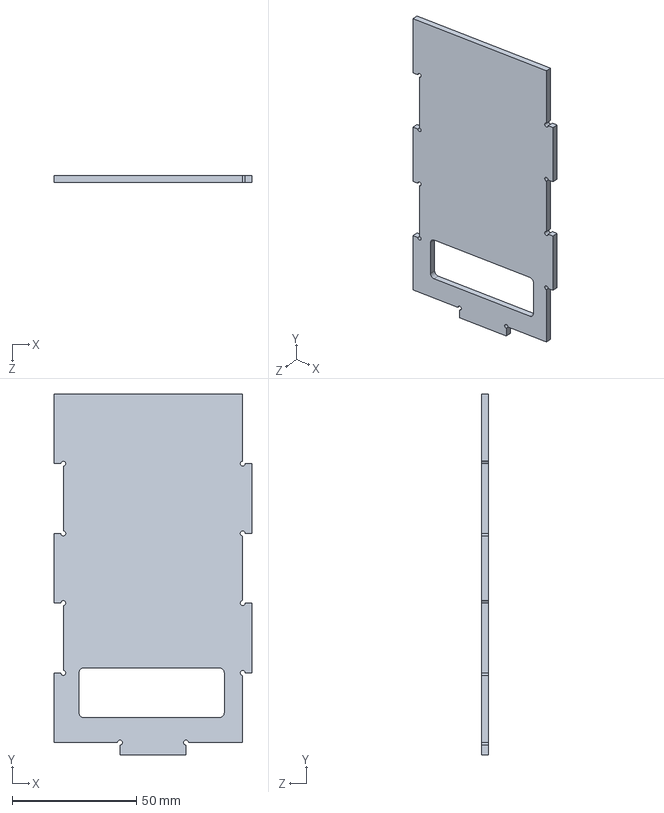
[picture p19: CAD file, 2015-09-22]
Hardware/Body/V�ike k�lg.SLDPRT
79.4 x 145.0 x 3.00 mm

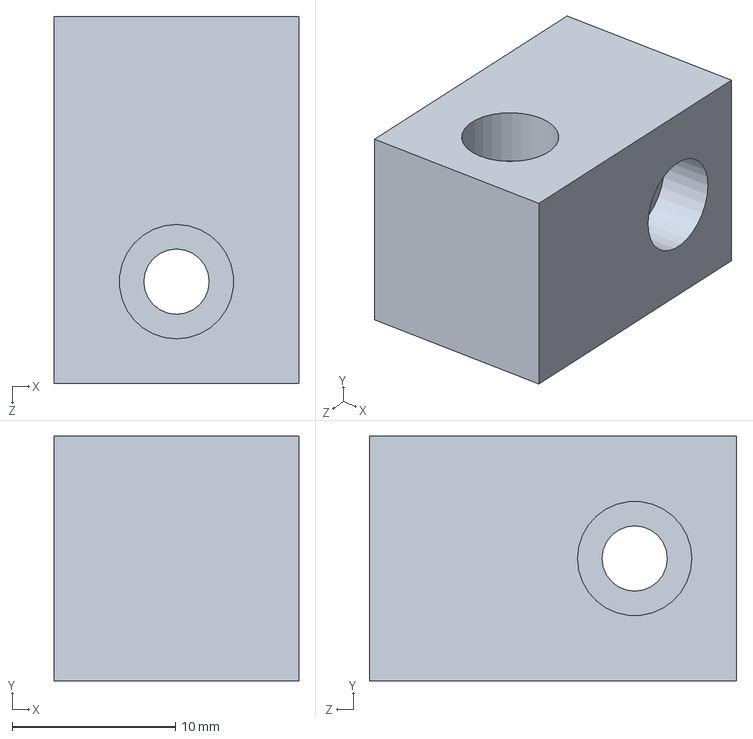
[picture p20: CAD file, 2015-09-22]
Hardware/Body/Kinnitusblokk.SLDPRT
15.0 x 15.0 x 22.5 mm

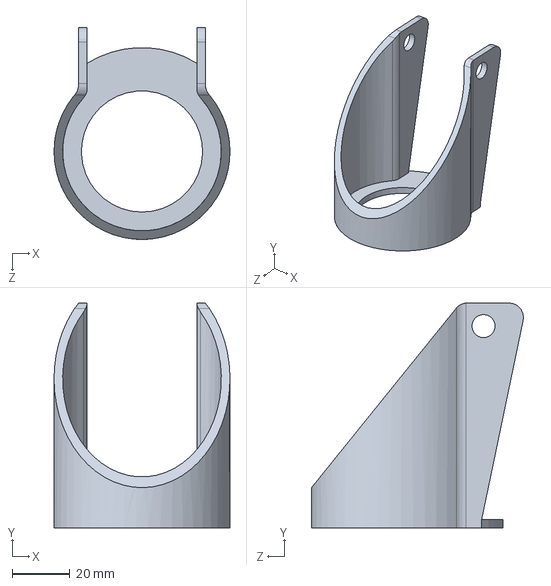
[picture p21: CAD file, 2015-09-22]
Hardware/Body/Eesratta raam.SLDPRT
61.0 x 78.0 x 73.5 mm

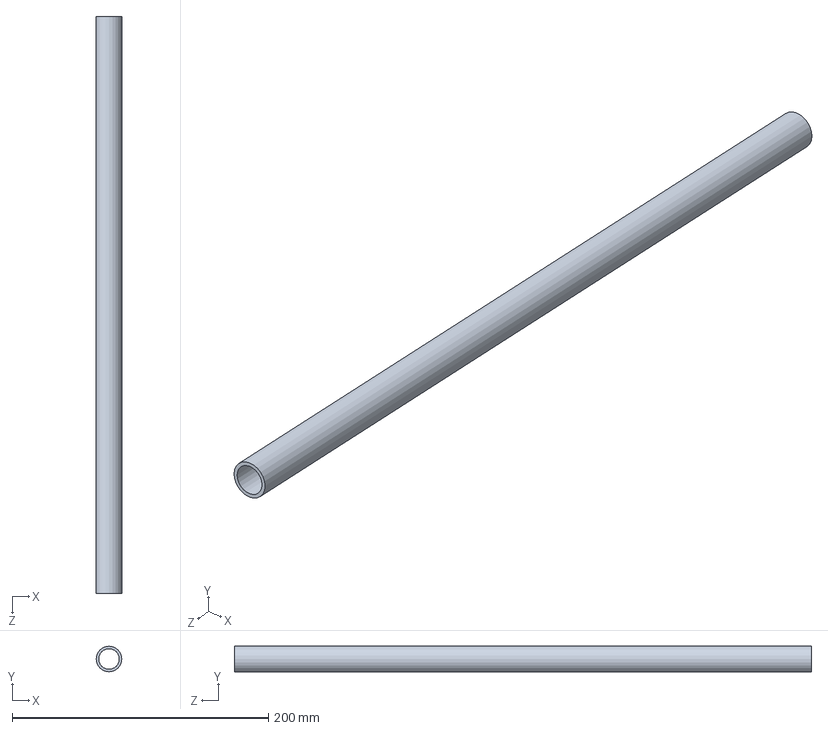
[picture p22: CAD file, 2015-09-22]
Hardware/Body/Telg.SLDPRT
20.0 x 20.0 x 450.0 mm

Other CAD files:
Hardware/Body/Aku.SLDPRT
Hardware/Body/Suur k�lg.SLDPRT
Hardware/Body/Siseplaat.SLDPRT
Hardware/Body/Ultraheli andur.SLDPRT
Hardware/Body/Alus.SLDPRT
Hardware/Body/Eesratta plaat.SLDPRT
Hardware/Body/Esiratas.SLDPRT
Hardware/Body/Katus.SLDPRT
Hardware/Body/Ratas.SLDPRT
Hardware/Body/Suur hammasratas.SLDPRT
Hardware/Body/Teljekinnitus.SLDPRT
Hardware/URF Box/URFBox.STL

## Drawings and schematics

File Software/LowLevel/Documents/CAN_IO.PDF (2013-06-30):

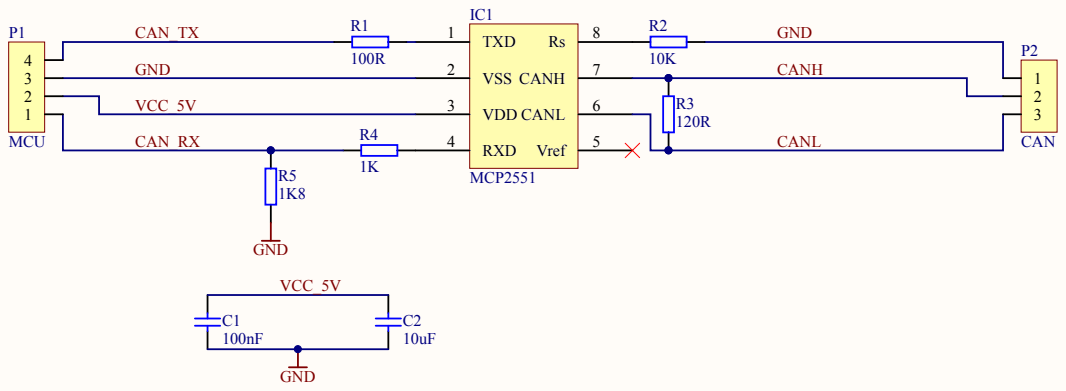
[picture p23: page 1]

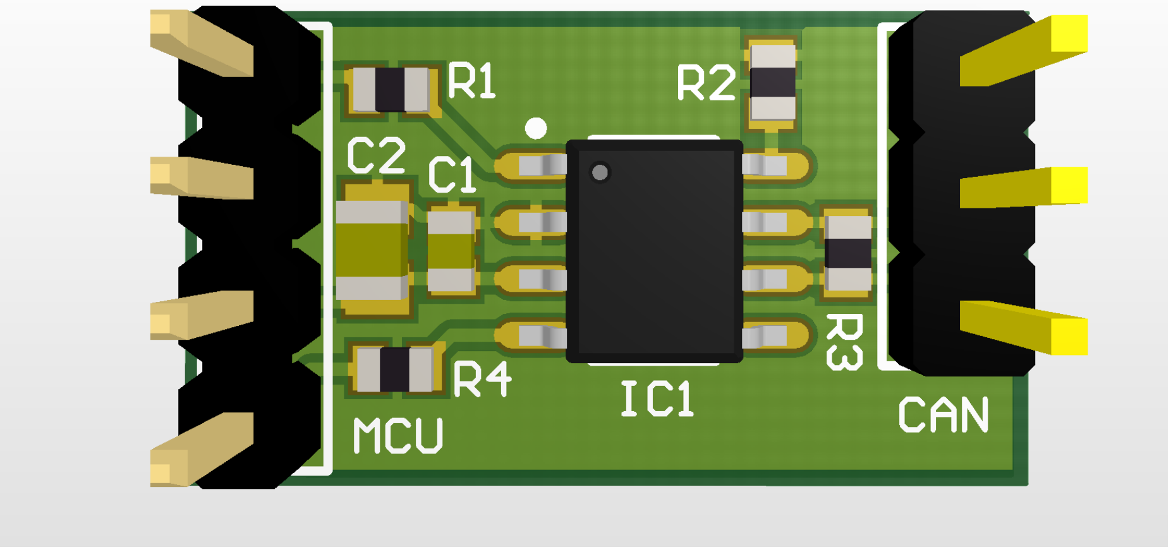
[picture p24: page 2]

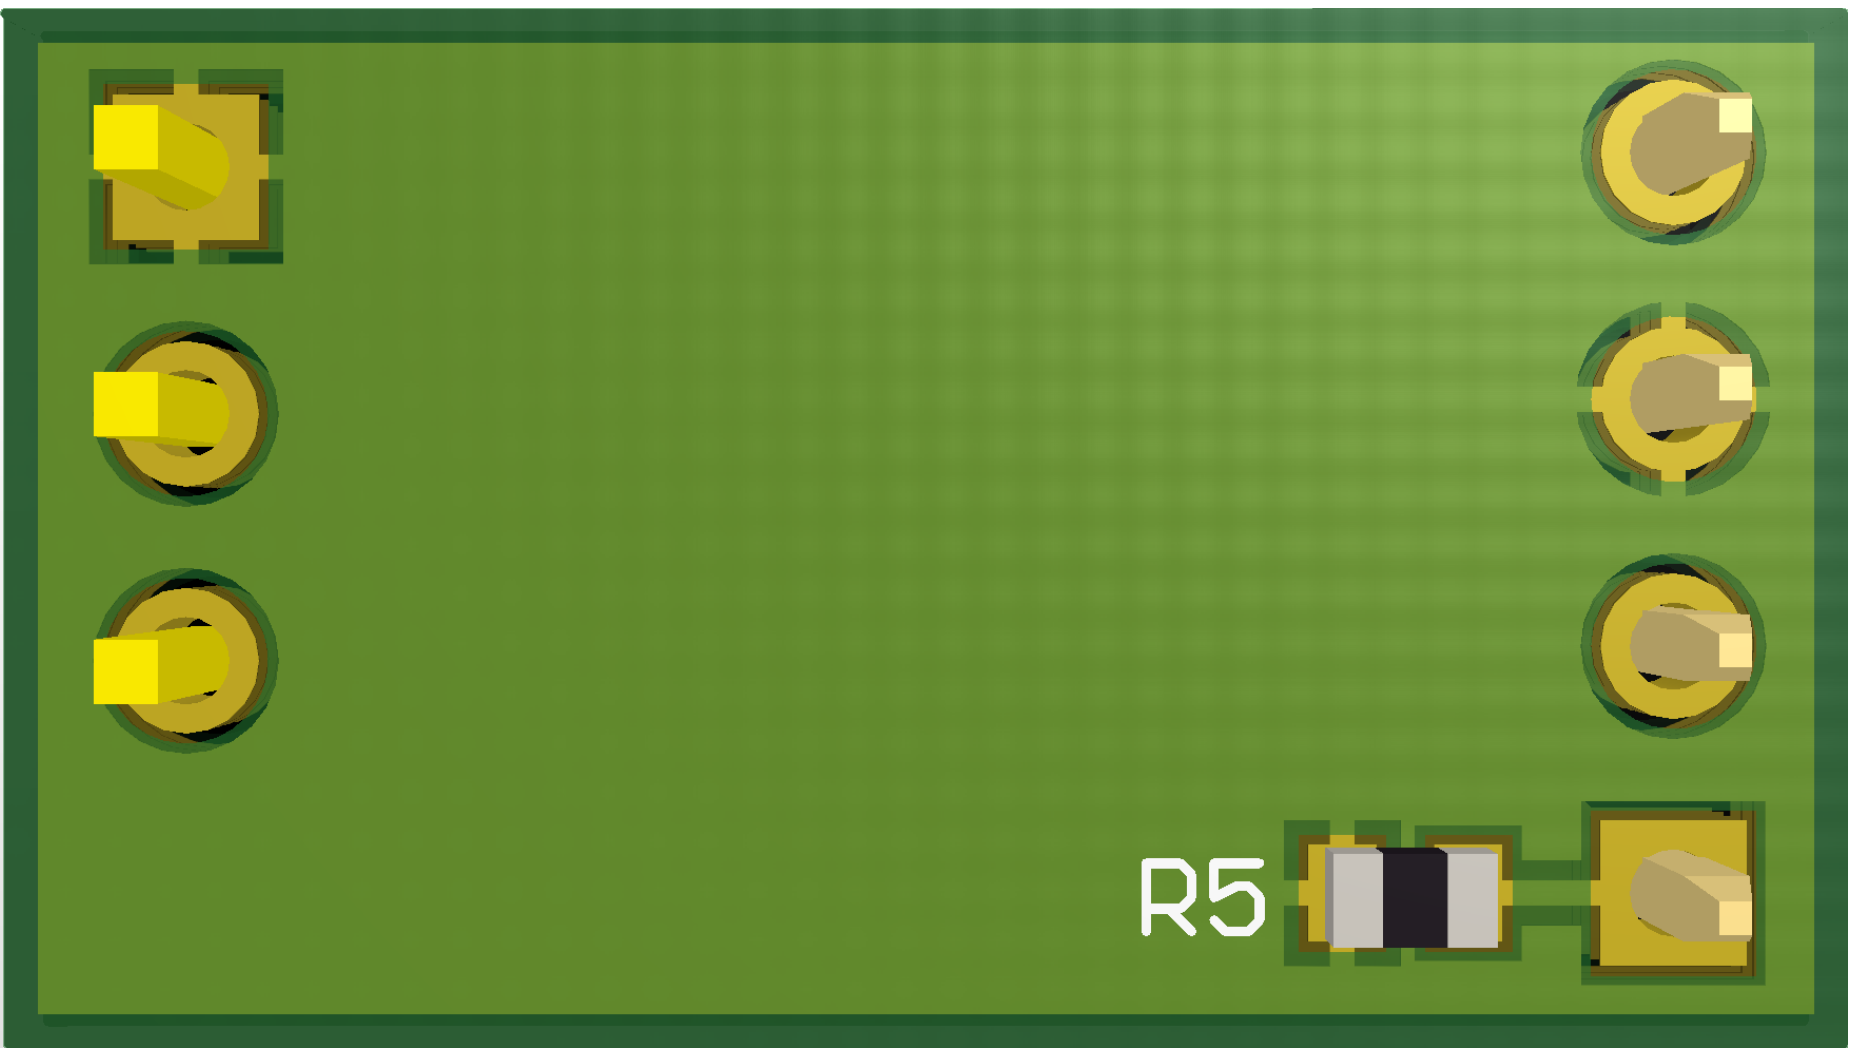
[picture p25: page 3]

Bill of Materials | CAN IO
Source Data From: | CAN_IO.PrjPCB
Project: | | CAN_IO.PrjPCB
Variant: | | None
Creation Date: 3.03.2013 | 16:19:57
Print Date: | 41336 | 41336,68054
Footprint | Comment | LibRef | Designator | Description | Quantity
C0603 C0805 SOIC-8 header-s4 header-s3 R0603 R0603 R0603 R0603 R0603 | 100nF 10uF MCP2551 MCU CAN 100R 10K 120R 1K 1K8 | C0603 C0805 MCP2551 con4p254 con3p254 R0603 R0603 R0603 R0603 R0603 | C1 | capacitor capacitor High-Speed CAN Transceiver con_4pin con_3pin Resistor Resistor Resistor Resistor Resistor | 1
| | | C2 | | 1
| | | IC1 | | 1
| | | P1 | | 1
| | | P2 | | 1
| | | R1 | | 1
| | | R2 | | 1
| | | R3 | | 1
| | | R4 | | 1
| | | R5 | | 1
Approved Notes | | | | | 10

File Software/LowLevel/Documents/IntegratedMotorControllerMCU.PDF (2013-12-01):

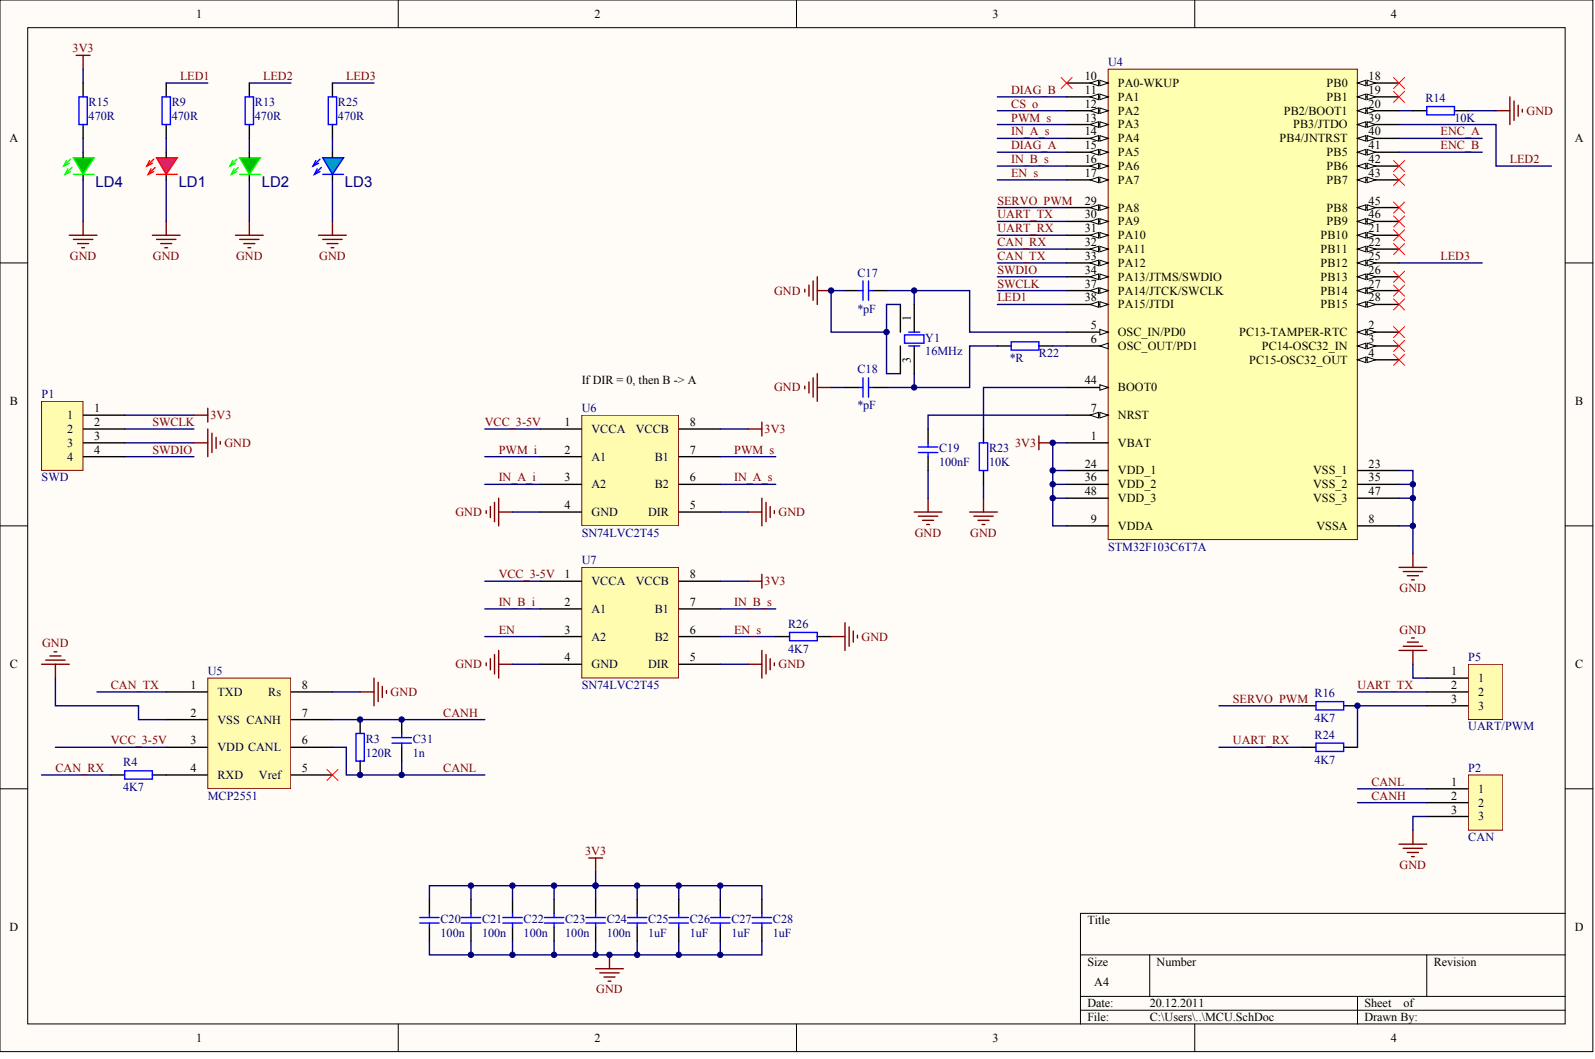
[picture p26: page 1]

VDD_1 24
VDD_2 36
VDD_3 48

VDDA 9

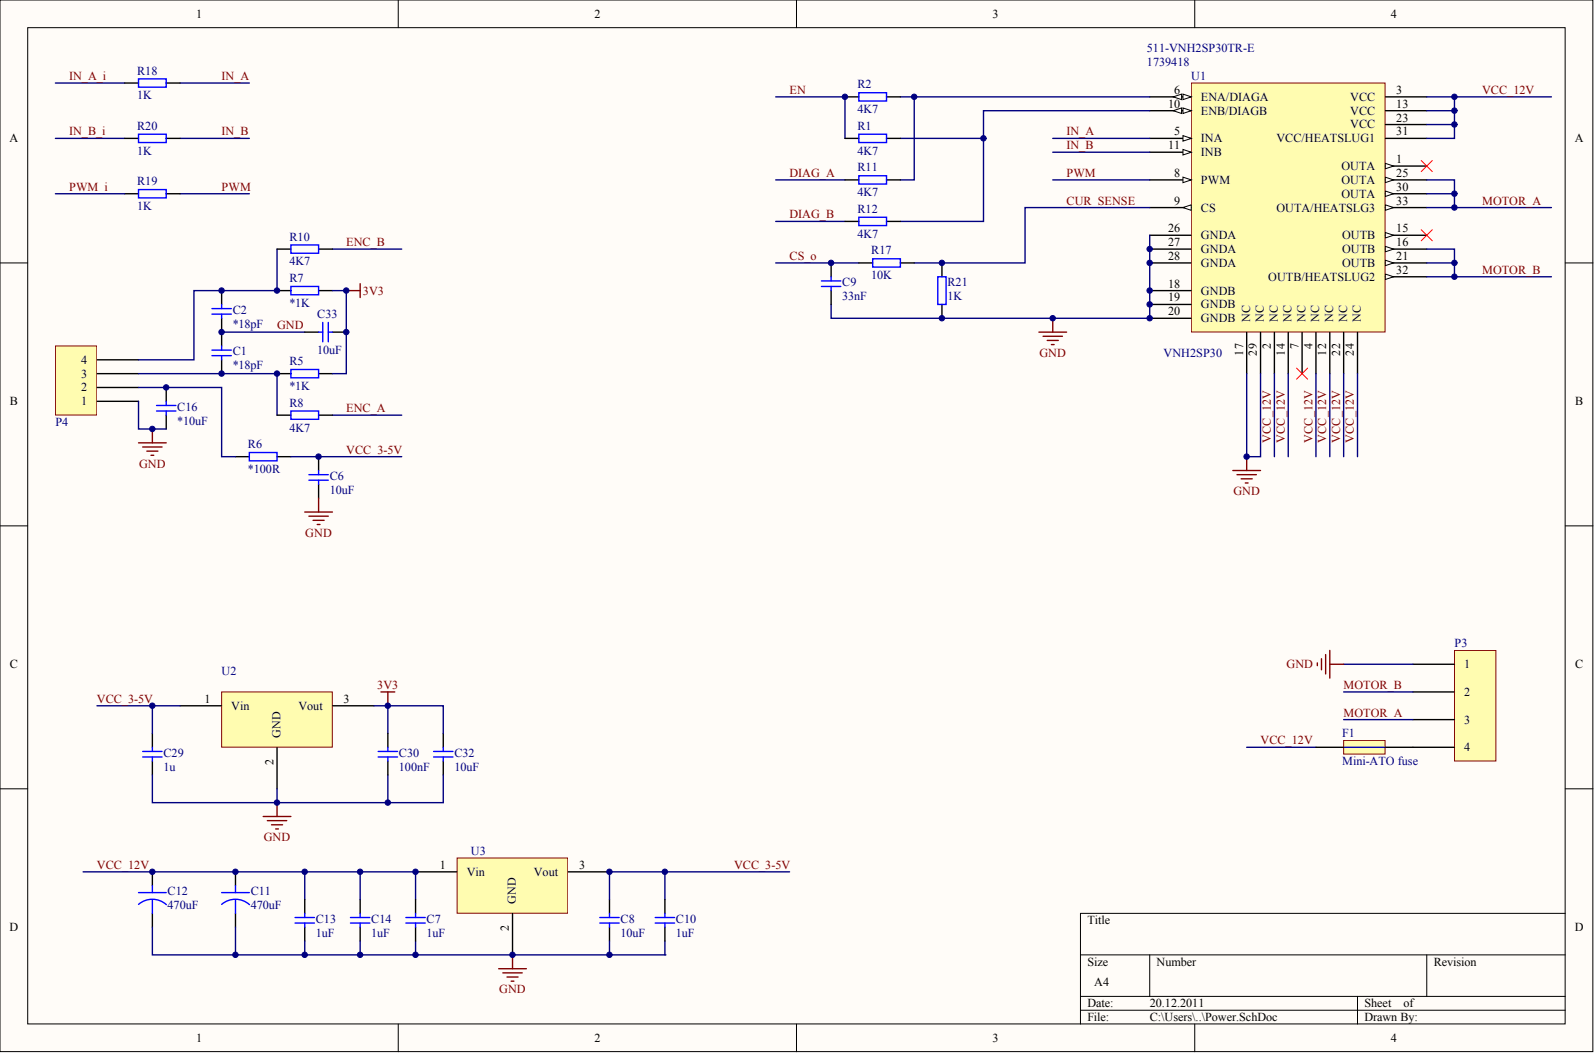
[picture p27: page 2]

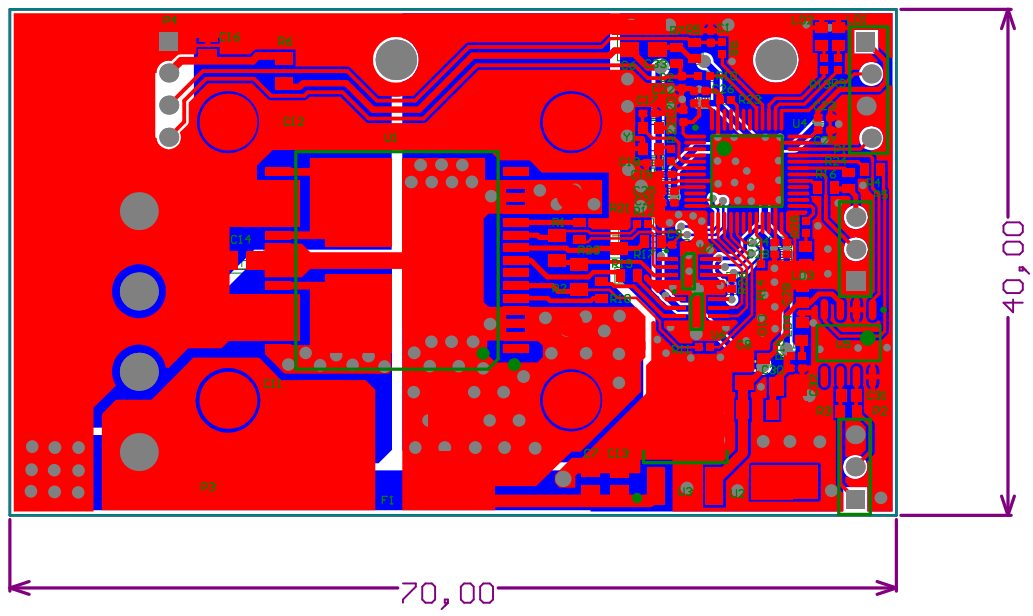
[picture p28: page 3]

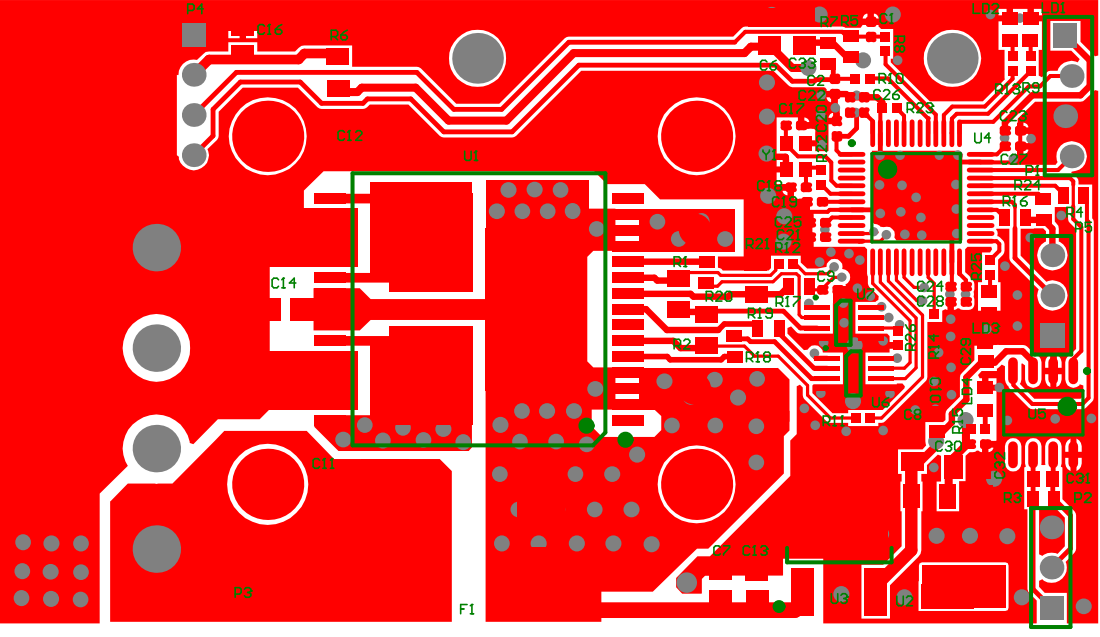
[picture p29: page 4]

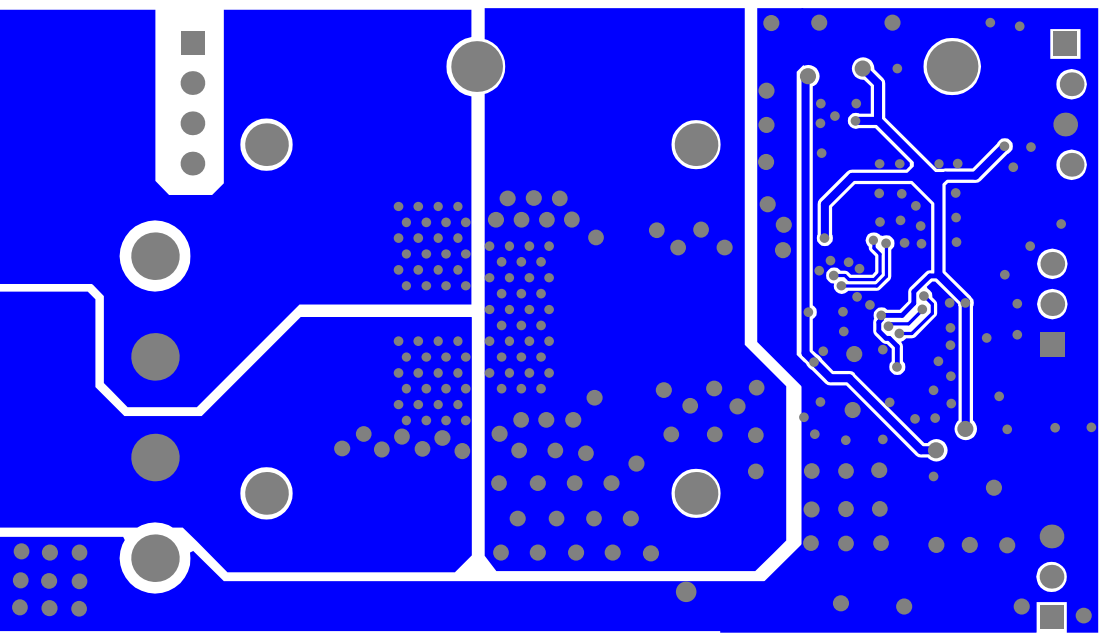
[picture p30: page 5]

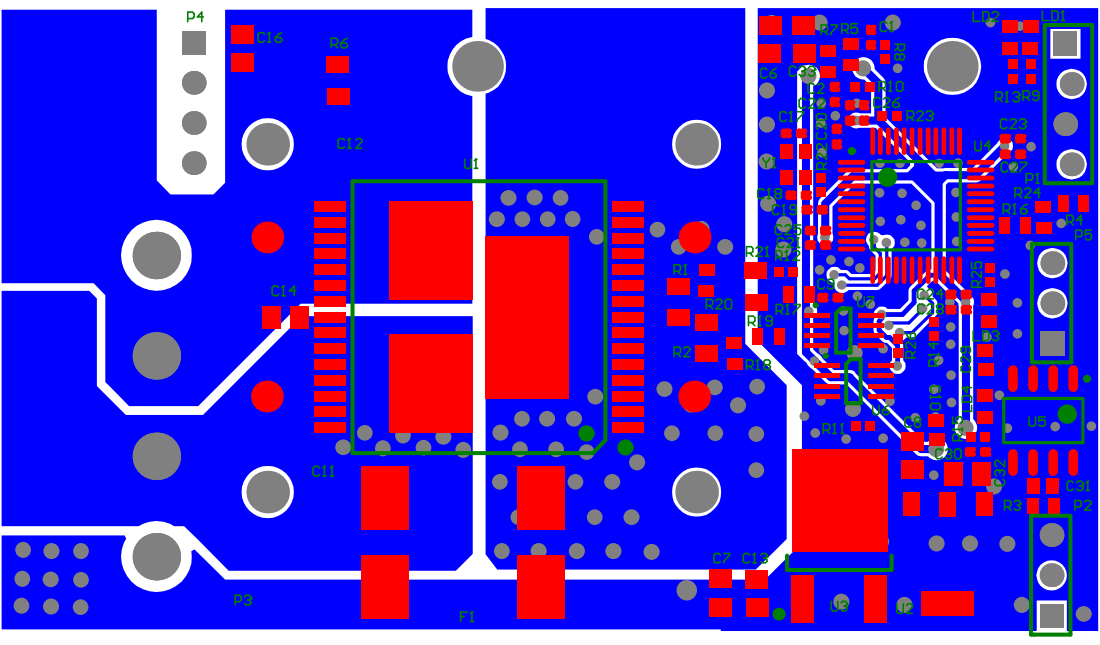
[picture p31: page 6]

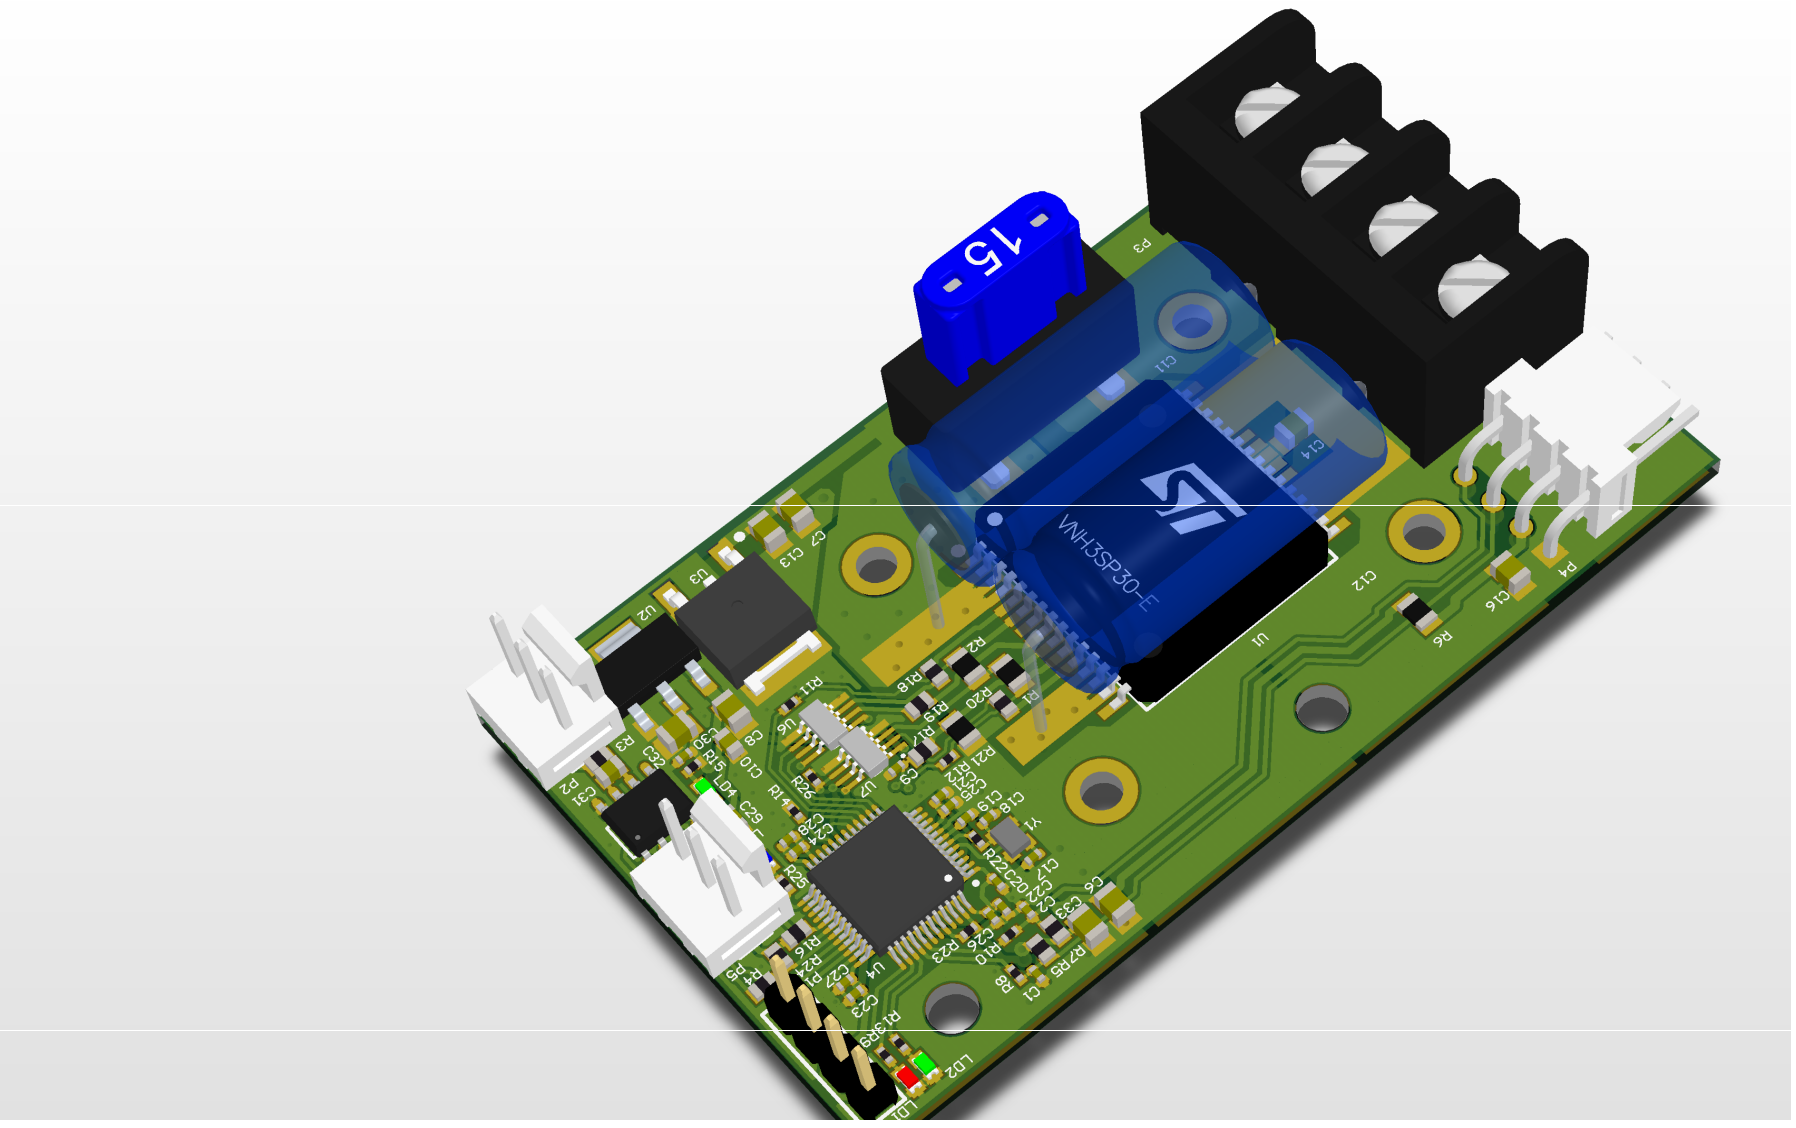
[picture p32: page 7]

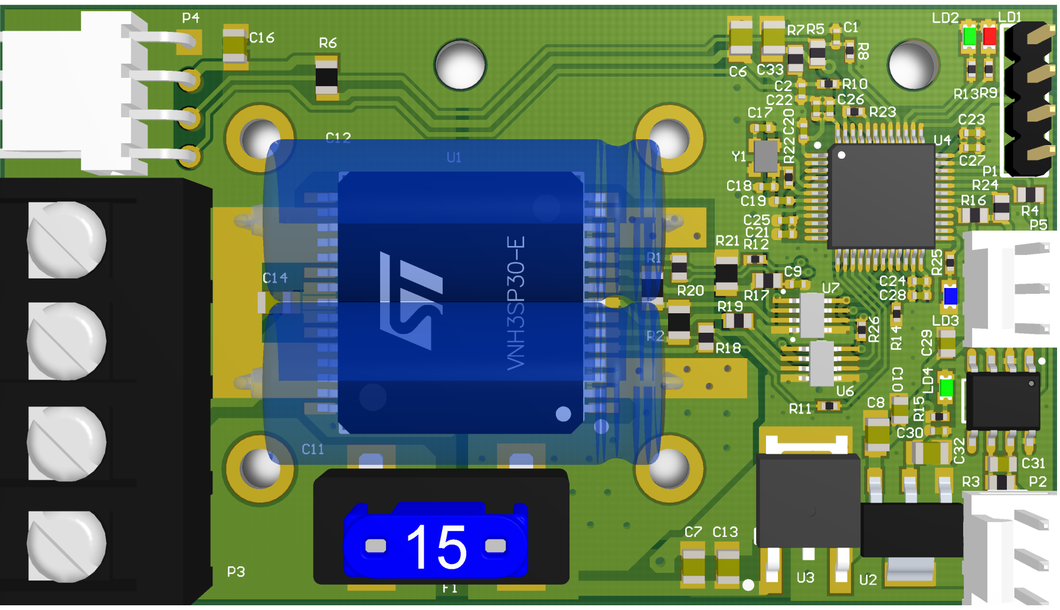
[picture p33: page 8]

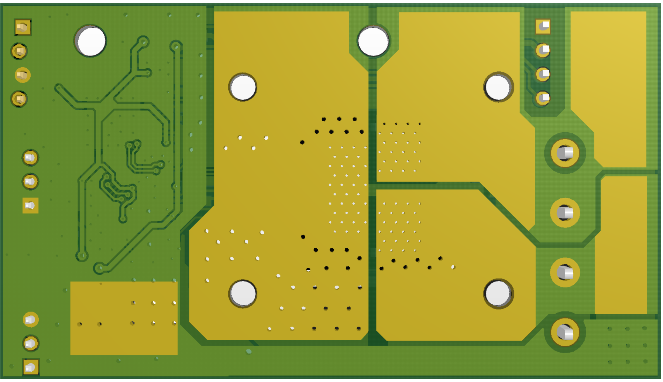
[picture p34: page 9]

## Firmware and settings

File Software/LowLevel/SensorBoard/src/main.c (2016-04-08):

/* Includes */
#include "stm32f4xx.h"
#include "stm32f4_discovery.h"
#include "TaskHandler.h"


int main(void)
{
	//Initialize task handler timer
	TaskHandler_init();
	// run infinitely
	while(1)
		TaskHandler_run();
	return 0;
}


/*
 * Callback used by stm32f4_discovery_audio_codec.c.
 * Refer to stm32f4_discovery_audio_codec.h for more info.
 */
void EVAL_AUDIO_TransferComplete_CallBack(uint32_t pBuffer, uint32_t Size){
  /* TODO, implement your code here */
  return;
}

/*
 * Callback used by stm324xg_eval_audio_codec.c.
 * Refer to stm324xg_eval_audio_codec.h for more info.
 */
uint16_t EVAL_AUDIO_GetSampleCallBack(void){
  /* TODO, implement your code here */
  return -1;
}

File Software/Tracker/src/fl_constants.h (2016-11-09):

#pragma once

#include <stdint.h>

const int kCandidateWidth = 64;
const int kCandidateHeight = 128;
const int kDepthWidth = 512;
const int kDeptHeight = 424;

const uint16_t kMinReliableDist = 500;
const uint16_t kMaxReliableDist = 4500;

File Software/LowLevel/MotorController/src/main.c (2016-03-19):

#include "stm32f10x.h"
#include "TASK_HANDLER.h"
#include "QEI.h"
#include "MODULATION.h"
#include "ANALOG.h"
#include "CAN.h"
#include "GPIO.h"

void init(void)
{
	//Enable AFIO (Alternate Function IO) clock
	RCC_APB2PeriphClockCmd(RCC_APB2Periph_AFIO, ENABLE);
	//Disable JTAG, but leave SWD enabled
	GPIO_PinRemapConfig(GPIO_Remap_SWJ_JTAGDisable,ENABLE);
}

int main()
{
  	init();
	vModulationHardwareInit();
    vAnalogHardwareInit();
    QEI_init();

  	TaskHandler_init();
	TaskHandler_run();
	return 0;
}

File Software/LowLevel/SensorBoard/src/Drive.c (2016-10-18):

#include "Drive.h"

#include "math.h"
#include "GPIO.h"
#include "DataLayer.h"

#include <stdlib.h>

typedef enum
{
	KP_X = 0,
	KI_X = 1,
	KD_X = 2,
	KP_W = 3,
	KI_W = 4,
	KD_W = 5,
	ACC_X = 6,
	ACC_W = 7
} PidParam;

typedef struct
{
	float yaw;
	float pitch;
	float roll;
} Euler;

static float kpX = 0.5f;
static float kiX = 0.5f;
static float kdX = 0.5f;
static float kpW = 0.3f;
static float kiW = 0.3f;
static float kdW = 0.3f;
static float accX = 2.0f;
static float accW = 1.0f;

static float kpX_t = 0.0f;  // temporary fields
static float kiX_t = 0.0f;
static float kdX_t = 0.0f;
static float kpW_t = 0.0f;
static float kiW_t = 0.0f;
static float kdW_t = 0.0f;
static float accX_t = 0.0f;
static float accW_t = 0.0f;

static int16_t priv_leftEncoder = 0;  //are 32-bits enough
static int16_t priv_rightEncoder = 0;
static float priv_speedX = 0;
static float priv_speedW = 0;
static float priv_gyroZ = 0;

static uint8_t updateParameters();
static void readEncoders();
static void stop();
static void readRequestedSpeeds();
static void readTurningSpeeds();
static void drive();

#define maxI 1000

uint8_t updateParameters()
{
	float value;
	PidParam param;
	uint8_t isUpdating;
	Bool result = DL_getData(DLParamPidValue, &value);
	result = result && DL_getData(DLParamPidParameter, &param);
	if (result)
	{
		switch(param)
		{
		case KP_X:
			kpX_t = value;
			break;
		case KI_X:
			kiX_t = value;
			break;
		case KD_X:
			kdX_t = value;
			break;
		case KP_W:
			kpW_t = value;
			break;
		case KI_W:
			kiW_t = value;
			break;
		case KD_W:
			kdW_t = value;
			break;
		case ACC_X:
			accX_t = value;
			break;
		case ACC_W:
			accW_t = value;
			break;
		default:
			break;
		}
	}

	if (DL_getData(DLParamPidUpdating, &isUpdating))
	{
		if (isUpdating)
		{
			uint8_t ack = 0xEE;
			kpX = kpX_t;
			kiX = kiX_t;
			kdX = kdX_t;
			kpW = kpW_t;
			kiW = kiW_t;
			kdW = kdW_t;
			DL_setDataWithForcedAsyncSend(DLParamRobotFeedback1, &ack);
			DL_setDataWithForcedAsyncSend(DLParamRobotFeedback2, &ack);
			return 1;
		}
		return 0;
	}
	else
		return 0;
}

void readEncoders()
{
	// TODO! Fail safe to add if one motor feedback not received then stop another
	int16_t left;
	int16_t right;
	if (DL_getData(DLParamMotor1EncoderClicks, &left)) // motor 1 is left
		priv_leftEncoder = left;
	if (DL_getData(DLParamMotor2EncoderClicks, &right))
		priv_rightEncoder = right;
}

void stop()
{
	int16_t left = 0;
	int16_t right = 0;

	left = 0;
	right = 0;
	DL_setData(DLParamMotor1RequestSpeed, &left);
	DL_setData(DLParamMotor2RequestSpeed, &right);
}

void readRequestedSpeeds()
{
	int16_t read;
	DL_getData(DLParamRequestTranslationSpeed, &read);
	priv_speedX = (float)read/10.0;
	DL_getData(DLParamRequestRotationSpeed, &read);
	priv_speedW = (float)read;
}

void readTurningSpeeds()
{
	int16_t gz;
	DL_getData(DLParamGyroZ, &gz);
	priv_gyroZ = (float)gz * 2000.0 / 32767.0;
}

float LimitVal(float val,float max)
{
	if (val > max)
	{
		return max;
	}
	else if (val < -max)
	{
		return -max;
	}
	return val;
}

int compare( const void* a, const void* b)
{
     float f_a = * ( (int*) a );
     float f_b = * ( (int*) b );

     if ( f_a == f_b ) return 0;
     else if ( f_a < f_b ) return -1;
     else return 1;
}

float filterGyroInput(float in)
{
	static float data[10] = {0,0,0,0,0,0,0,0,0,0};
	static int dp = 0;

	float sum;
	int i;

	data[dp] = in;

	dp++;
	dp %= 10;

	//sort
	qsort( data, 10, sizeof(float), compare );


	sum = 0;
	// get average
	for (i = 2; i < 8; i++)
	{
		sum += data[i];
	}

	return sum / 6;


}

void controlRangeLimit(float *val,float min,float max)
{
	if (*val  < min)
	{
		*val = min;
	}
	else if (*val  > max)
	{
		*val = min;
	}
}

void drive()
{
	static float fwd_speed = 0, turn_speed = 0;
	static int16_t rightSpeedOld = 0, leftSpeedOld = 0;
	float posX = 0, posW = 0;
	float errLX, errRX, errW;
	static float iLX = 0,iRX = 0,iW = 0;
	static float LasterrLX = 0, LasterrRX = 0, LasterrW = 0;
	float dLX = 0,dRX = 0,dW = 0;


	static float turnSpeedOld = 0;

	// Linear acceleration, TODO - do not allow negative

	if (GPIO_inputValue(STOP_BUTTON) == INPUT_OFF)
	{
		rightSpeedOld = 0,
		leftSpeedOld = 0;
		turnSpeedOld = 0;
		DL_setDataWithForcedAsyncSend(DLParamMotor1RequestSpeed, &leftSpeedOld);
		DL_setDataWithForcedAsyncSend(DLParamMotor2RequestSpeed, &rightSpeedOld);


		// reset PID
		iLX = 0;
		iRX = 0;
		iW = 0;
		LasterrLX = 0;
		LasterrRX = 0;
		LasterrW = 0;
		dLX = 0;
		dRX = 0;
		dW = 0;

		return;
	}

	if (priv_speedX < 0)
	{

		if (fwd_speed != priv_speedX)
		{
			if (priv_speedX < fwd_speed)
			{
				fwd_speed += accX*2;
			}
			else
			{
				fwd_speed += accX*0.25;
			}

			if (fwd_speed > priv_speedX)
			{
				fwd_speed = priv_speedX;
			}
		}
	}
	else
	{
		if (fwd_speed != priv_speedX)
		{
			if (priv_speedX > fwd_speed)
			{
				fwd_speed -= accX;
			}
			else
			{
				fwd_speed -= accX*2;
			}

			if (fwd_speed < priv_speedX)
			{
				fwd_speed = priv_speedX;
			}
		}
	}

	/*

	if(fwd_speed < priv_speedX)
	{
		if (priv_speedX >= 0)
		{
			fwd_speed += accX;
		}
		else
		{
			fwd_speed = priv_speedX;
		}

	}
	else if(fwd_speed > priv_speedX)
	{
		if (priv_speedX >= 0)
		{
			fwd_speed = priv_speedX;
		}
		else
		{
			fwd_speed -= accX;
		}
	}

	*/
	// Rotational acceleration
	if(turn_speed < priv_speedW)
		turn_speed += accW;
	else if(turn_speed > priv_speedW)
		turn_speed -= accW;
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

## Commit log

2013-02-10 First commit with sensorBoard code, where HC-SR04 sensor is showing distance in cm on LCD.
2013-02-24 CaseCatcher tool added to project. Sensors message added to PC module. SensorBoard code for 4 URF sensors. Pins not configured.
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2013-05-01 Measuring all four URF sensors, but writes out over UART only 2-4 results.
2013-06-02 First solution in CAN communication. Sending just a test CAN message and receives messages also.
    [bit time.xlsx]
2013-06-02 Added UART packet handling, so now data should be passed from CAN to UART and vice versa.
2013-06-09 URF andurite ümberpaigutus PINout osas. Kasutajaliidese programm kuvab URF andurite näite. Lisatud exceli dokument kirjeldamaks STm32 pinnide kasutust.
    [STM32_pinout.xlsx]
2013-06-09 USART2 tööle. Sensorite andmed saadetakse arvutisse üle xRF-i. NB! Korraga saab hetkel töös olla ainult üks UART/USART.
    [STM32_pinout.xlsx]
2013-06-30 Support for U/S32 data in CAN and in USART. User button activates CAN speed check sequence to detect correct CAN speed.
    [bit time.xlsx]
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2013-07-25 Added MotorController project.
    [bit time.xlsx]
2013-08-11 GPIO moodul lisatud, LED pandi vilkuma. Vea parandus TaskHandler moodulis. PID konstandid kirjutatud otse flashi.
2013-09-09 Muudetud roboti kuja ja lisatud suurendus pooleli on veel sensorite paigutus ja nende asukoha muutmine.
2013-09-15 Momendil toetus kolme URF jaoks. Igale oma taimer ning interrupti eraldi välja lülitamine.
2013-09-16 Tugi 8 URF anduri jaoks. Hetkel kõik veel ei tööta. CAN protokoll sai dokumendis muudetud, vaja koodis ka muudatusi teha.
    [STM32_pinout.xlsx]
2013-09-30 8 URF sensorit tööle.
    [STM32_pinout.xlsx]
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2013-12-08 Puuduvate failide lisamine. Koodi puhastamine ja ebavajalike failide kustutamine.
    [SpineCommCAN.cpp]
2013-12-30 Mootorikontrollerites on kiiruse sõnumi timeout. Kui 10x perioodi jooksul pole kiiruse sõnumit tulnud, siis pannakse mootorid seisma. Parandatud CAN sõnumite vastuvõtmine sensori plaadil (STm32F4 kit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
    [STM32_pinout.xlsx]
2014-02-01 Kiirendusanduri kood lisatud STm32 kontrollerile. TaskHandlerisse sisse ehitatatud init funktsioonide võimalus, et iga mooduli saaks TaskHandler ise vajadusel välja kutsuda.
    Remote PC koodis lisatud sujuv kiirendamine ja aeglustamine. Roboti juhtimine
    läbi kinemaatika klassi.
2014-05-12 väike parandus biti ajastuse arvutamise tekstis
    [bit time.xlsx]
2014-06-02 Parandatud URF sensori lugemist. Juurde arvestatud error lugem. Teiste sensorite koodi tuleb muuta sarnaselt.
    [Sensor.c]
2014-06-08 Parandused URF sensorite lugemises.
    [STM32_pinout.xlsx]
2014-07-15 VisionBoard koodi lisamine. Üle I2C liidese Pixy kaamerast andmete lugemine ning andmepuhvri parsimine objektide leidmiseks. Viimane testimata veel.
2014-07-27 TrackedObject sõnum lisatud. Mõned ebavajalikud CAN/UART sõnumid eemaldatud. VisionBoard moodulis kasutusele võetud InterfaceConfig. DL-st andmete panemine paketidesse sai muudetud, nii et oleks ühin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
2014-08-01 Mitteperioodiliste sõnumite käsitlemine tehtud. Parandatud mõningaid vigu. PacketHandler moodulit pole enam vaja - InterfaceHandler teeb töö ära üldisemal kujul, nii et UARTi ja CANi koodid saavad ka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
2014-08-09 VisionBoard edastab CAN-i Pixy kaameras leitud objekti.
    [STM32_pinout.xlsx]
2014-08-09 SensorBoard sai uuendatud CAN, UART liideste uue koodiga. Parandatud sai mitmeid vigu.
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2015-02-17 Lisatud kunagi unustatud failid.
    [GPIO.c]
2015-06-07 Lisatud juurde UART4 suhtlus. USART moodul suudab suhelda nüüd mõlema liidesega (USART2 ja UART4). Liideste definitsioone sai muudetud, et ka Kinectist saadetud järgitava objekti info jõuaks remote a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
2015-06-16 Lisatud Hardware kaust ja ultraheli andurite detaili 3d mudel
    [URFBox.SLDPRT, URFBox.STL]
2015-07-14 Parandatud üks viga uint16/int16 andmete salvestamisel andmekihti. Hetkel UART4 kaudu vastuvõtmine välja kommenteeritud.
2015-08-12 Lisatud sügavuspildi edastamise paketid sensorplaadi moodulile. Lisatud tugi ka kahest USART-st andmete lugemiseks samal ajal.
2015-08-12 Kustutatud mitte kasutusel olevat koodi. Lisatud UInt32/Int32 tugi andmete saatamiseks üle UART-i. Lisatud sügavuspildi sõnumi vastuvõtmine. Likvideeritud kompilaatori poolt edastatud hoiatused.
2015-08-18 Sõnumipuhvri andemosa tegin suuremaks (32 baiti). Uus DepthRaw sõnum lisatud ka paketi käsitlejasse. Whitespace muudatused kogu SpineCommCAN faili ulatuses.
    [SpineCommCAN.cpp]
2015-08-25 Akumooduliga suhtlemiseks on I2C1 ja I2C3.
    [STM32_pinout.xlsx]
2015-08-25 Added batteryManagmentSystem shecmatic and PCB files
    [BalancerQauge.SchDoc, BatteryManagementSystem.PcbDoc, BatteryManagementSystem.PrjPCB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]
2015-09-07 RxNE staatust ei tohi nullida, see tehakse automaatselt staatus registrit lugedes. Kasutusele tuleb I2C3 liides akumooduliga (power) suhtlemiseks.
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2015-09-22 Lisatud kere 3D part failid.
    [Aku.SLDPRT, Alus.SLDPRT, Eesratta plaat.SLDPRT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]
2015-10-11 Eraldi DataHandler moodul lisatud, mis uuendab perioodiliste sõnumite aega, nii et kommunikatsioonimoodulid (CAN, UART) saavad aru, millal peaks neid saatma.
    UART moodul saadab mootorite infot, nii UART4 kui ka USART2.
    Kustutatud mõned kasutud sõnumid (MotorPID, Motor3RequestSpeed)
2015-10-14 Lisatud readme faili, milliseid OpenCV ja Boost versioone on vaja eelnevalt installida.
2015-10-25 Lisatud mõned projekti dokumendi failid.
    [J�rgija projekti taotluse- ja aruandevorm.xls]
2015-12-10 Kuna andmete logimine hakkab toimuma läbi Zotaci, siis ei ole tarvidust enam TrackedObject ja DepthRaw sõnumite järele. Lisatud servode juhtimiseks mõeldud sõnum (E0). Lisatud USB kood, et teha virtu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
2015-12-14 Eelnevalt unustatud usb failid lisatud. Lisatud sõnum kaamera servode juhtimiseks. Esialgne servode juhtimise kood, mis on testimata.
    [DataLayerConfig.c, GPIO.c, TaskHandler.c]
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2016-02-02 Lisatud tudengiprojekti aruanne.
    [2015_projektikonkurssi_eelarve.xlsx, J�rgija_taotluse_ja_aruandevorm.xlsx, Kanded.xlsx]
2016-02-02 Failid liigutatud 2015 tundengiprojekt kausta
    [J�rgija projekti taotluse- ja aruandevorm.xls]
2016-02-09 Made main loop with fixed timing (20 ms). Added algorithm handling code, added buttons to start and stop algorithms. Made separate struct (CommOutput) for outgoing data.
2016-02-09 Fixed Linux build. Removed unused filter code.
2016-02-16 Added algorithm move to test rotating with IMU sensor. Fixed some issues with sending data to serial.
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2016-03-19 Updated motor controller motor driving so that requested speed given via CAN message is directly forwarded to PWM. No ramp and pid logic in between. Motor rotation clicks are given, but unfortunately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
    [CAN.c, DataLayerConfig.c, main.c]
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2016-04-19 Fixed camera conrtol message period to be async.
    [PacketConfig.cpp]
2016-04-19 Moved data handler functionality to data layer module. PID parameter update returns message containing 0xEE. Fixed bug that invalidity flags remained true even if packet was set waiting.
    [DataHandler.c, Drive.c, SpineCommCAN.cpp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]
2016-05-22 Robot feedback data is stored to file. Idea is to log system parameters during PID tuning process.
    Replace Quaternion message with gyro euler degrees message.
    Extended robot feedback message.
    [DataLayerConfig.c, Drive.c, InterfaceConfig.c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]
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2016-09-19 Updated vision board with latest DataLayer and InterfaceHandler code. Added vision board test project and added test to check that vision board passes through distance sensor data from can to usb. Fi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
    [CAN.c, DataHandler.c, DataLayerConfig.c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]
2016-09-19 Renamed testGlobal to projectConfig. Added missing test files under SensorBoardTest. Renamed parameters releated to gyro packet
    [CAN.c, DataLayerConfig.c, Drive.c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]
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2016-09-19 Added fix to pass async packets between different interfaces. InterfacePacket structs contains PacketDescritor instead of Packet now.
    [CAN.c, InterfaceConfig.c]
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2016-09-27 Refactor Configuration Files Both sensor and PID settings are now saved to robot.ini.
    If a reset is necessary, delete robot.ini and let it be generated again.
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2016-10-04 Updated sensor board pinout document with stop button
    [STM32_pinout.xlsx]
2016-10-07 Removed arrow actions from Kinematics class to followerui class. Cleaned up Kinematics class by removing unused code.
    Added keyboard off state to followerui, so it is possible to disable
    keyboard actions.
    Issue #9
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2016-10-11 Resolve #8 - Implement Testing Routine Implements a testing routine into the Configure object and window. Along with new UI elements.
    Keyboard commands are toggled off if testing is started,
    and the configuration UI is made unusable until testing ends.
    Testing can be stopped by the user clicking the "STOP TEST!" button.
    Test parameters are added to the log file if the file is written for testing.
    Logging now writes the current input translation and rotation speeds along with the other 4 bits of data.
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2016-10-18 Fix osx build. Add target to camera degrees translation.
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2016-10-18 fixed servo x and y
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2016-10-21 Add depth image flipping.
    [fl_constants.h]
2016-10-28 Update ignore file to not show untracked files
    [Järgija_taotluse_ja_aruandevorm.xlsx]
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2016-11-02 Chartdisplay WIP Implemented file scanning at startup and selection.
    Implemented the basis for rudimentary data selection.
    RedrawLines() should edit the visibility of different lines, whenever the data selection is updated. It should call setVisibility(bool) for the different line series, with the argument being tied to the whitelist array.
    It's currently a mess of two arrays to make sense of user input.
    It may also have issues with accessing non-existent indeces, which causes crashing. Calling chart_.removeSeries() (I think that's the helper), or or removing series invidiually, completely destroys the series object. Even if it's stored elsewhere.
    Also has an apparent memory leak (?) with c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
2016-11-08 chartdisplay - fix file duplication bug Chartdisplay duplicated the files list whenever you switched off from it and then back to it.
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
